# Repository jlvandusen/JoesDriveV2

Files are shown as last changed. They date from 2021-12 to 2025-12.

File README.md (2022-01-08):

# JoesDriveV2
* Shared Code Base for Joe's Drive V2 using AdaFruit Feather CPUs and SND Boards
* This will support a complete PCB delivered solution to simplify and provide cost savings for future development.
* utilizes ESP32 and Feather based CPUs
* Simplified but adaptable Dome Controls
* Land, Sea and Air control schemas supporting Wifi, BT and more...
* This will contain all the code for my Joe's drive V2 setup.

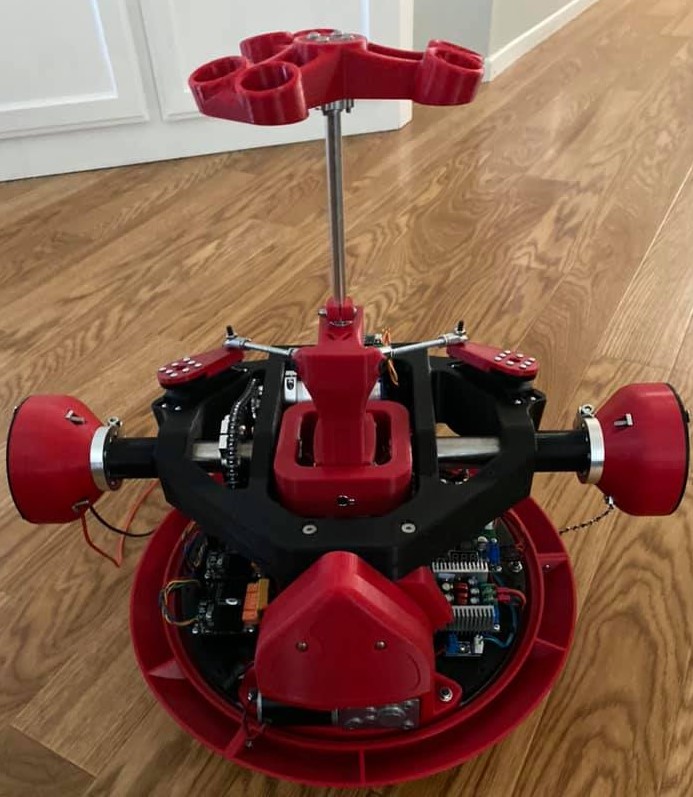
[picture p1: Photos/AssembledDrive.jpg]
JoesDrivev2


## Hardware setup
This drive is everything including the kitchen sink, remote starter, easy to configure ESP32 to Move or Xbox controllers (no other hardware needed), Single PCB board with all needed connections

### ESP32 Huzzah
The ESP32 Huzzah Feather is the main brains of the drive, and it is responsible for handling the remote functions and reading the IMU sub-board from the serial terminals.

### 32u4 Proto M0
Currently utilizes a second Feather 32u4 M0 for offloading remaining serial ports for Dome specific controls over serial.

### trinket Pro Mini - IMU reader
IMU locks are the thing of the past

### ESP32 Huzzah Dome Controller
Utilizes easy to configure ESPNOW technologies to communicate between body and dome - no more wifi or pairing garbage.

## New Features
The following are the new features that I have added into my drive to make it more usable.
Feature | Description
------- | -----------
All-In_One PCB | The Main board has buck converters built right in with all necessary connections over PIN and JST XH.  48V in and supports 5v, 6v and 9v outputs.
i2c Sound Control | Utilizes standard (non pin triggered) i2c sound controls allowing for full flexibility and adaptable sound choices based on button combination and actions.
CHain Drive! | The main drive is handled by chain drive to solve slipping seen in previous versions as well as to provide a more stable drive experience.
S2S Gearing | Utilizes gear for stable side to side controls (similar to Bruton's design)
ENC Dome Control | Utilizes ENC built in motor controls for exact directional control of dome rotation.
v2 Flywheel | Very low profile (higher than the battery compartment - thus allowing for out of ball testing and weight disbursement.
DFRobot 0601 | Using the DFRobot Motor Driver 0601 H Bridge Motor driver
Mp3 Qwiic/i2c trigger | Code that drives the custom Mp3 trigger for full sound controls via multi combinations

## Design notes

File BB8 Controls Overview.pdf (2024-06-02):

## BB8 SHADOW Movement controls

Your first controller when paired and turned on, will become your drive controller
The second controller when paired and turned on will become your dome controller
Key movement controls explained
You will hold the 2 nav controllers in your left and right hands, for the convenience of this instructional, we will represent your left hand as the dome controls and your right hand as the drive controls.
Movement does not occur until the Drive Safety feature has been enabled. This is done by pressing the PS button the drive controller. It’s a toggle, so pressing will enable or disable the drive systems for safety reasons.

## Drive Controller commands

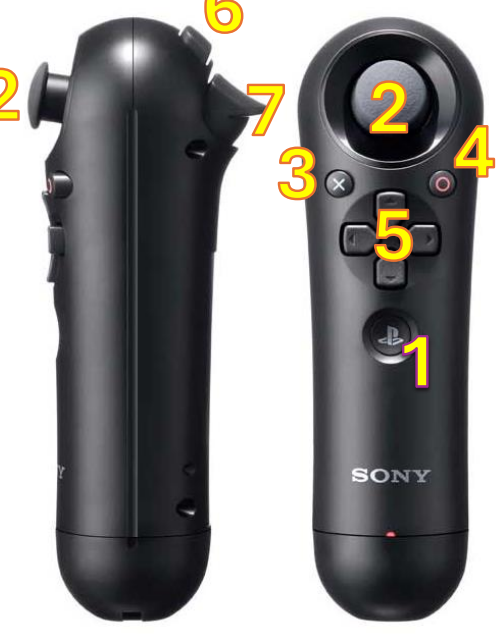
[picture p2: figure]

1. PS = Drive Enable/Disable safety
2. Forward/Backward = Forward or backward drive movement, Left/Right = Side to Side left or right for steering Pressing in the joystick will reverse the drive direction. By default its forward, if pressed will reverse all controls.
3. X =
4. O =
5. Digital pad up, down, left and right will play sounds, NOTE: the pad up will be random sounds.
6. L1 = Modifier (enabling Dome Spin movements)
7. L2 =

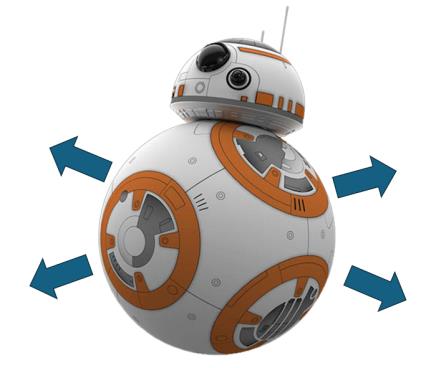
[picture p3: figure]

## Dome Controller commands

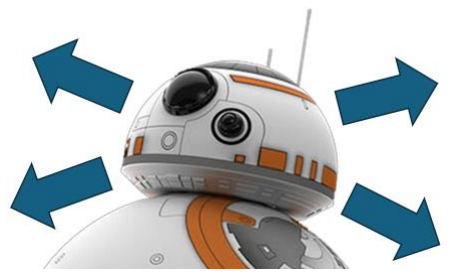
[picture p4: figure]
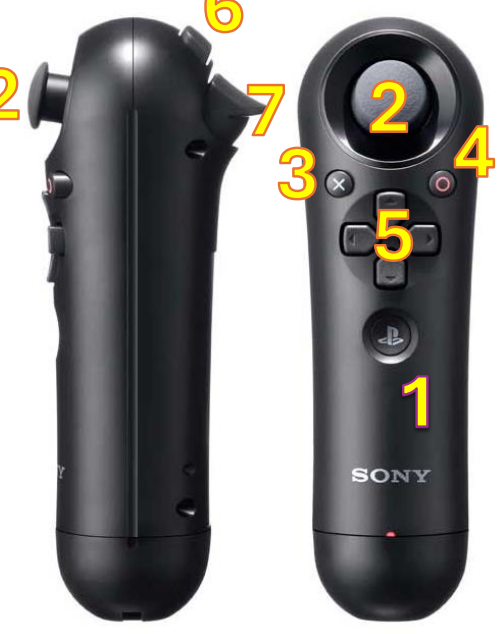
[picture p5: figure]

1. PS = Drive Enable/Disable safety
2. Forward/Backward = Forward or backward dome movement, Left/Right = left and right dome movement. Pressing in the joystick will enable dome servo mode and the navigation now on the drive controller will be forced to turning only left or right 40 degrees from center.
3. X =
4. O =
5. Digital pad up, down, left and right will play sounds, NOTE: the pad up will be random sounds.
6. L1 = Modifier (enabling Gyro movements using the drive controller left or right)
7. L2 =

### Saving offsets

When pressing digital pad (5) up on both controllers, will enable save of all current placements (potentiometer and IMU offsets).

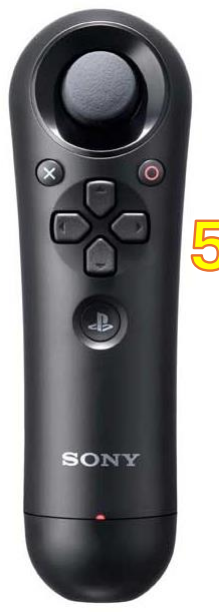
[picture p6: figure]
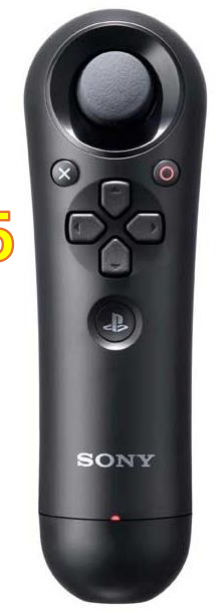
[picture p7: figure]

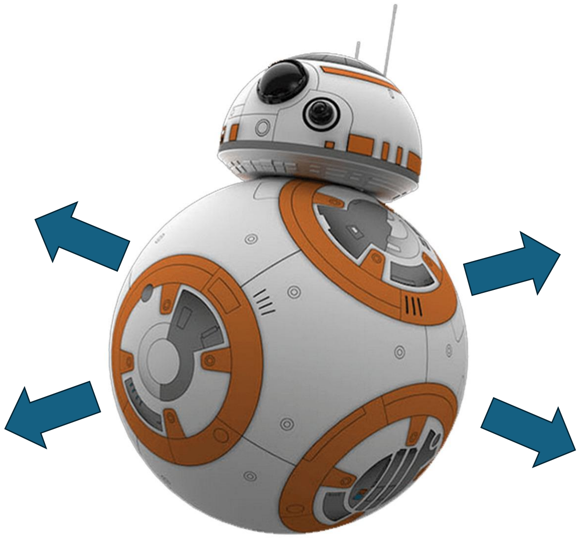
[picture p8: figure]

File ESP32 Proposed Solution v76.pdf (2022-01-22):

# Joe’s Drive v2

# The Solution consists of 3 PCB boards

1. Main Board – this regulates power from a single 48v - 12v battery to 5v, 6v or 9v outputs, it has all the necessary connectors to quickly wire to DFRobot H Bridge motor controllers and all required sensors. It utilizes 2 CPUs which segregate duties between dome or main body related motors and sensors
(Feather 32u4 Proto M0 or 32u4 Basic Proto | Feather 32u4 RF Series AND Feather ESP32 HUZZAH Series processors).

NOTE: There are 6 options given depending upon secondary 32u4 and which MP3 trigger you wish to use

2. IMU/MPU Board – this connects via Serial and consists of dedicated CPU (trinket m0) as well as MPU6050 series that regulates Pitch, Tilt and yaw movement on the system.
3. Dome board – this communicates via ESP32NOW to the Main Board and controls LEDs in the dome only. Future adaption of motion sensor and distance sensors.

# Version 7.1/7.5/7.6

# OPTION 1: 32u4 PROTO M0 and i2C MP3 Trigger

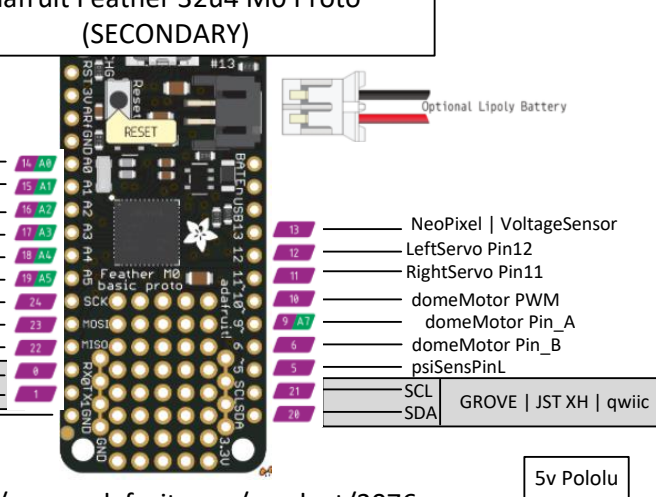
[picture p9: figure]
NeoPixel | VoltageSensor; domeMotor Pin_B; domeMotor Pin_A; psiSensPinL; LeftServo Pin12 RightServo Pin11 domeMotor PWM; SCL; SDA; GROVE | JST XH | qwiic; 5v Pololu; (SECONDARY)
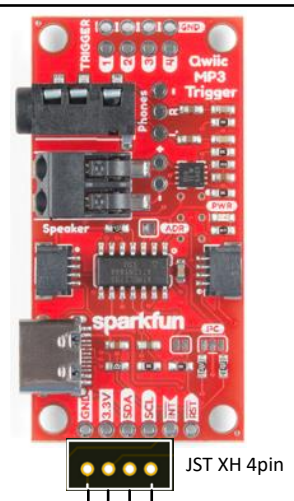
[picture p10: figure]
JST XH 4pin
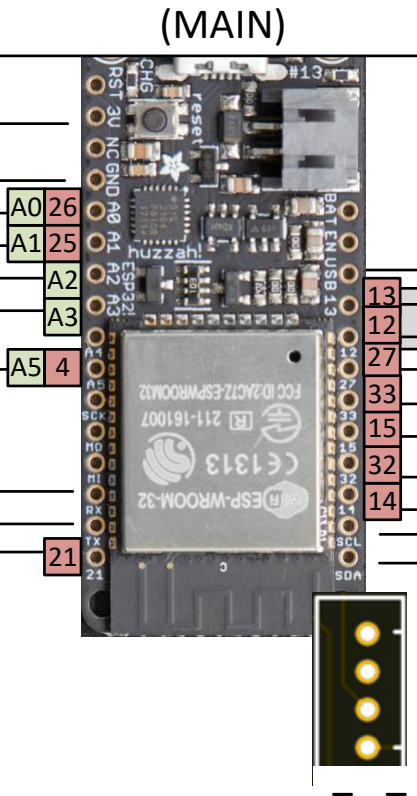
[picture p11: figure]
(MAIN)

S2SPOT

drivepin1

S2SPin1

drivepin2

S2SPin2

Trinket
(Serial1)

To 32u4
(Serial2)

MotorEncPinA
MotorEncPinB

VCCSensor

HallMonitor

To ESP32
(Serial1)

ESP32
(Serial1)

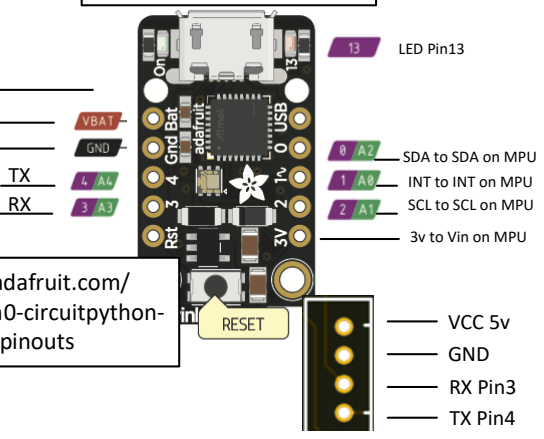
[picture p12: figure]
SCL to SCL on MPU; SDA to SDA on MPU; INT to INT on MPU; 3v to Vin on MPU; TX Pin4; RX Pin3; GND; VCC 5v; LED Pin13

TX

## MPU6050

## Adafruit Trinket M0

5V

GND

SCL

SDA

5v

https://learn.adafruit.com/mpu6050-6-dof-accelerometer-and-gyro/pinouts

https://learn.adafruit.com/adafruit-trinket-m0-circuitpython-arduino/pinouts

GND

INT

i2C

12/24/48v In
5v Out

GND Out
GND In

Bat on 32u4,
Trinket and
ESP32
And Outputs

S2S_PWM

Drive_PWM

GND

+ 3.3v

+5v Input

## https://www.adafruit.com/product/3076

lLogicPIN

battPin (26)
psiPIN (25)

(Serial1)

sLogicPIN

GND

## Adafruit ESP32 HUZZAH32 Feather (DOME)

FlyMotor PWM
FlyMotor Pin_A
FlyMotor Pin_B
SCL
SDA
GND

GND 3.3V SDA SCL
To Feather 32u4

Sparkfun QWIIC MP3 TRIGGER

VCC 5v

GND

TX Pin17 ESP32

RX Pin16 ESP32

## To Trinket (MPU)

## To ESP32 (MAIN)

12/24/48v In
9v/6v Out

GND Out
GND In

To Left/Right
Servo and
Output

6v/9v Pololu

## Adafruit ESP32 HUZZAH32 Feather

## Adafruit Feather 32u4 M0 Proto

# OPTION 2: 32u4 Basic Proto and i2C MP3 Trigger

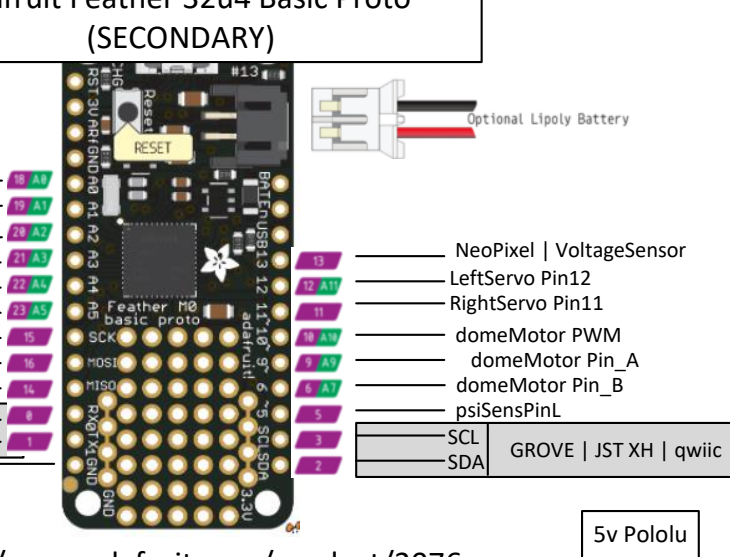
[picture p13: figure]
NeoPixel | VoltageSensor; domeMotor Pin_B; domeMotor Pin_A; psiSensPinL; LeftServo Pin12 RightServo Pin11 domeMotor PWM; SCL; SDA; GROVE | JST XH | qwiic; 5v Pololu; (SECONDARY)

S2SPOT

drivepin1

S2SPin1

drivepin2

S2SPin2

Trinket
(Serial1)

To 32u4
(Serial2)

MotorEncPinA
MotorEncPinB

VCCSensor

HallMonitor

To ESP32
(Serial1)

ESP32
(Serial1)

TX

## MPU6050

## Adafruit Trinket M0

5V

GND

SCL

SDA

5v

https://learn.adafruit.com/mpu6050-6-dof-accelerometer-and-gyro/pinouts

https://learn.adafruit.com/adafruit-trinket-m0-circuitpython-arduino/pinouts

GND

INT

i2C

12/24/48v In
5v Out

GND Out
GND In

Bat on 32u4,
Trinket and
ESP32
And Outputs

S2S_PWM

Drive_PWM

GND

+ 3.3v

+5v Input

## https://www.adafruit.com/product/3076

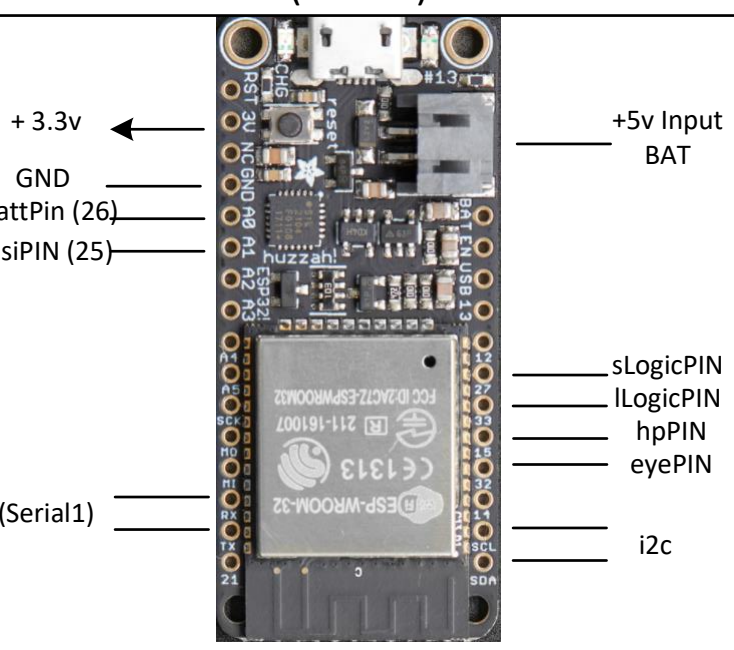
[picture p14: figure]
+5v Input; BAT; hpPIN eyePIN

lLogicPIN

battPin (26)
psiPIN (25)

(Serial1)

sLogicPIN

GND

## Adafruit ESP32 HUZZAH32 Feather (DOME)

FlyMotor PWM
FlyMotor Pin_A
FlyMotor Pin_B
SCL
SDA
GND

GND 3.3V SDA SCL
To Feather 32u4

Sparkfun QWIIC MP3 TRIGGER

VCC 5v

GND

TX Pin17 ESP32

RX Pin16 ESP32

## To Trinket (MPU)

## To ESP32 (MAIN)

12/24/48v In
9v/6v Out

GND Out
GND In

To Left/Right
Servo and
Output

6v/9v Pololu

## Adafruit ESP32 HUZZAH32 Feather

## Adafruit Feather 32u4 Basic Proto

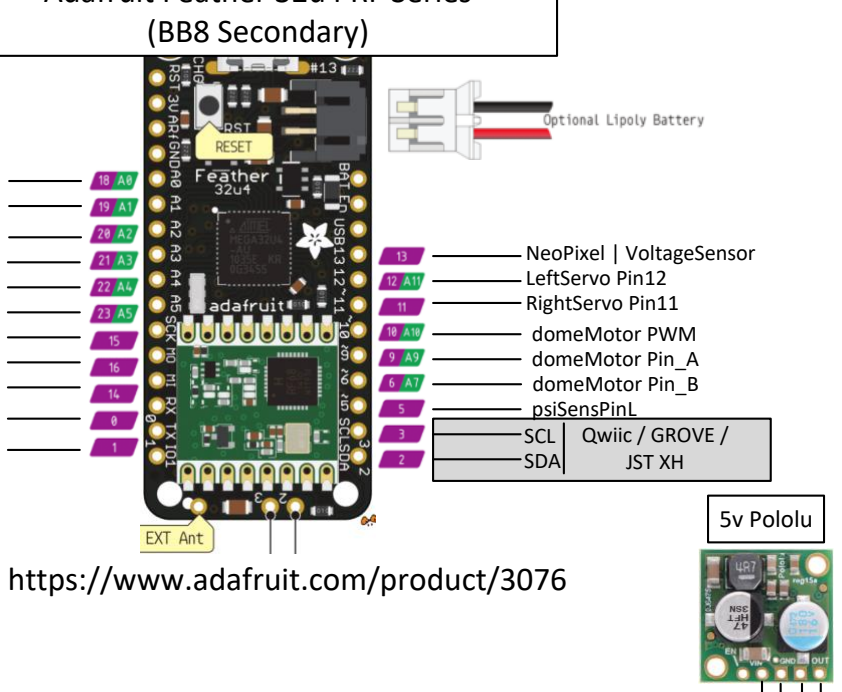
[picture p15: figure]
NeoPixel | VoltageSensor; domeMotor Pin_B; domeMotor Pin_A; psiSensPinL; LeftServo Pin12 RightServo Pin11 domeMotor PWM; https://www.adafruit.com/product/3076; SCL SDA; Qwiic / GROVE / JST XH; 5v Pololu; (BB8 Secondary)

MotorEncPinA
MotorEncPinB
HallMonitor

ESP32
(Serial1)

# OPTION 3: 32u4 RF and i2C MP3 Trigger

S2SPOT

drivepin1

S2SPin1

drivepin2

S2SPin2

Trinket
(Serial1)

To 32u4
(Serial2)

ESP32
(Serial1)

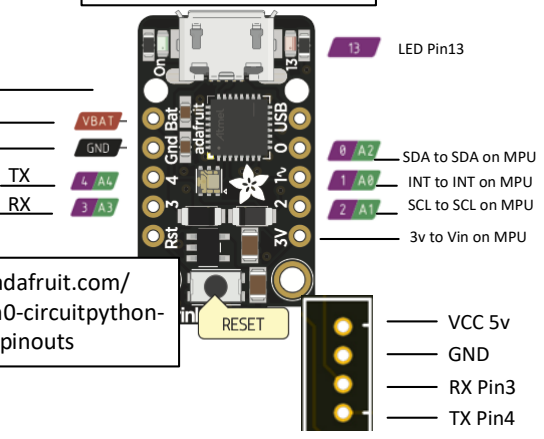
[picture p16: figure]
SCL to SCL on MPU; SDA to SDA on MPU; INT to INT on MPU; 3v to Vin on MPU; TX Pin4; RX Pin3; GND; VCC 5v; LED Pin13

TX

## MPU6050

## Adafruit Trinket M0

5V

GND

SCL

SDA

5v

https://learn.adafruit.com/mpu6050-6-dof-accelerometer-and-gyro/pinouts

https://learn.adafruit.com/adafruit-trinket-m0-circuitpython-arduino/pinouts

GND

INT

i2C

12/24/48v In
5v Out

GND Out
GND In

Bat on 32u4,
Trinket and
ESP32
And Outputs

S2S_PWM

Drive_PWM

GND

+ 3.3v

+5v Input

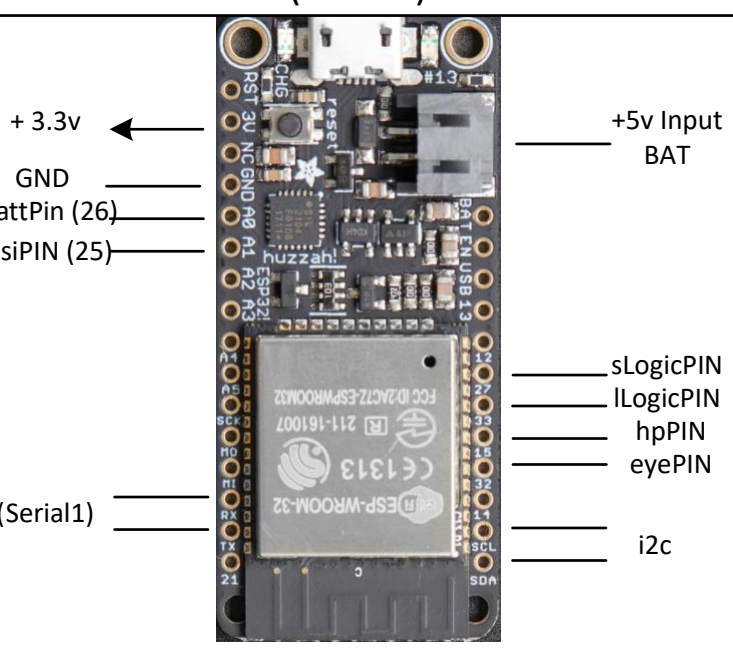
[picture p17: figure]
+5v Input; BAT; hpPIN eyePIN

lLogicPIN

battPin (26)
psiPIN (25)

(Serial1)

sLogicPIN

GND

## Adafruit ESP32 HUZZAH32 Feather (DOME)

FlyMotor PWM
FlyMotor Pin_A
FlyMotor Pin_B
SCL
SDA
GND 3.3V SDA SCL
To Feather 32u4

Sparkfun QWIIC MP3 TRIGGER

VCC 5v

GND

TX Pin17 ESP32

RX Pin16 ESP32

## To Trinket (MPU)

## To ESP32 (MAIN)

12/24/48v In
9v/6v Out

GND Out
GND In

To Left/Right
Servo and
Output

6v/9v Pololu

## Adafruit ESP32 HUZZAH32 Feather Adafruit Feather 32u4 RF Series

# OPTION 4: 32u4 PROTO M0 and ADAFRUIT MUSIC MAKER FEATHERWING

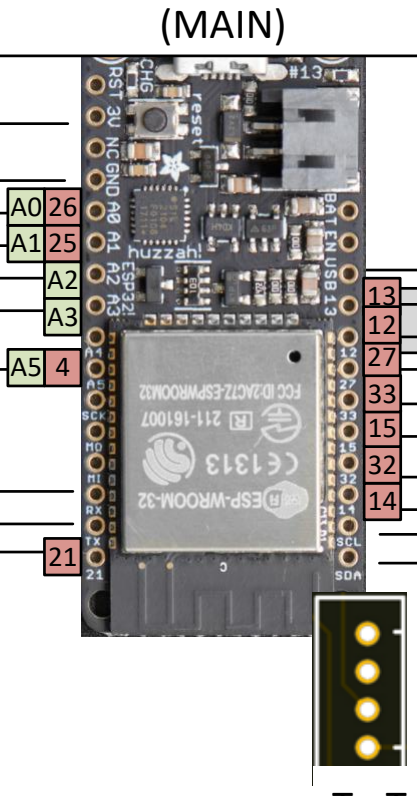
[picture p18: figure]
(MAIN)

S2SPOT

drivepin1

S2SPin1

drivepin2

S2SPin2

Trinket
(Serial1)

To 32u4
(Serial2)

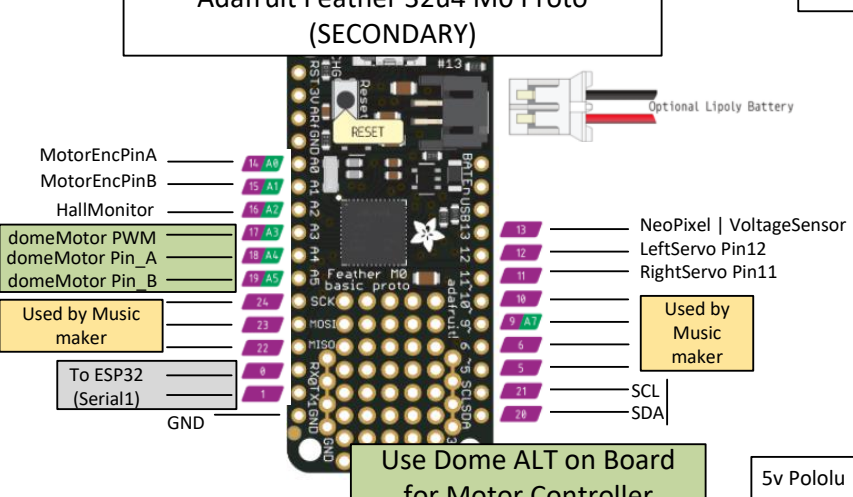
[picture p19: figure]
NeoPixel | VoltageSensor; domeMotor Pin_A; LeftServo Pin12; RightServo Pin11; To ESP32 (Serial1); SCL SDA; GND; 5v Pololu; (SECONDARY); domeMotor PWM; Use Dome ALT on Board; Used by Music maker

MotorEncPinA
MotorEncPinB

domeMotor Pin_B

HallMonitor

ESP32
(Serial1)

TX

## MPU6050

## Adafruit Trinket M0

5V

GND

SCL

SDA

5v

https://learn.adafruit.com/mpu6050-6-dof-accelerometer-and-gyro/pinouts

https://learn.adafruit.com/adafruit-trinket-m0-circuitpython-arduino/pinouts

GND

INT

i2C

12/24/48v In
5v Out

GND Out
GND In

Bat on 32u4,
Trinket and
ESP32
And Outputs

S2S_PWM

Drive_PWM

GND

+ 3.3v

+5v Input

lLogicPIN

battPin (26)
psiPIN (25)

(Serial1)

sLogicPIN

GND

## Adafruit ESP32 HUZZAH32 Feather (DOME)

FlyMotor PWM
FlyMotor Pin_A
FlyMotor Pin_B
SCL
SDA

ADAFRUIT VS105 Feather

VCC 5v

GND

TX Pin17 ESP32

RX Pin16 ESP32

## To Trinket (MPU)

## To ESP32 (MAIN)

12/24/48v In
9v/6v Out

GND Out
GND In

To Left/Right
Servo and
Output

6v/9v Pololu

## Adafruit ESP32 HUZZAH32 Feather

## Adafruit Feather 32u4 M0 Proto

## for Motor Controller

X
X
X

X
X
X
X

# OPTION 5: 32u4 Basic Proto and ADAFRUIT MUSIC MAKER FEATHERWING

S2SPOT

drivepin1

S2SPin1

drivepin2

S2SPin2

Trinket
(Serial1)

To 32u4
(Serial2)

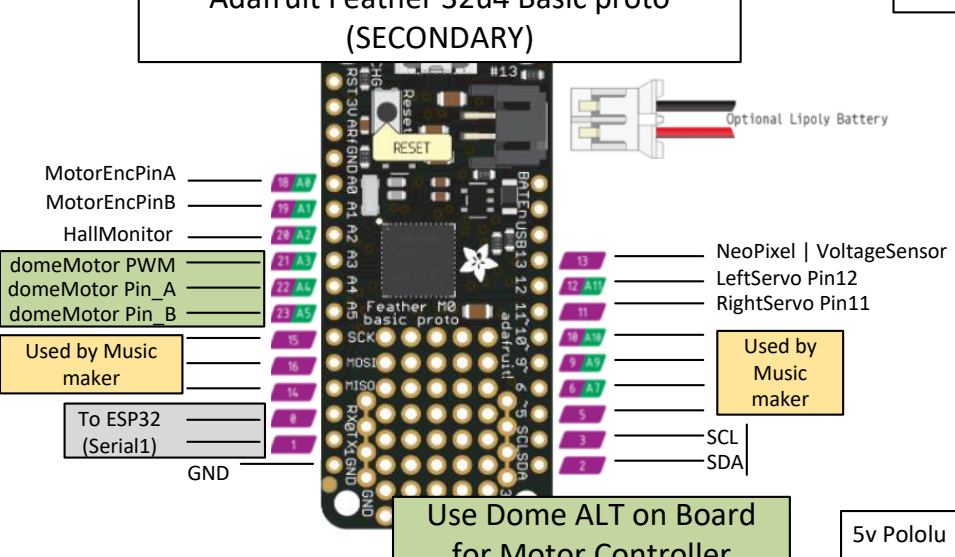
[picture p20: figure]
NeoPixel | VoltageSensor; domeMotor Pin_A; LeftServo Pin12; RightServo Pin11; To ESP32 (Serial1); SCL SDA; GND; 5v Pololu; (SECONDARY); domeMotor PWM; Use Dome ALT on Board; Used by Music maker

MotorEncPinA
MotorEncPinB

domeMotor Pin_B

HallMonitor

ESP32
(Serial1)

TX

## MPU6050

## Adafruit Trinket M0

5V

GND

SCL

SDA

5v

https://learn.adafruit.com/mpu6050-6-dof-accelerometer-and-gyro/pinouts

https://learn.adafruit.com/adafruit-trinket-m0-circuitpython-arduino/pinouts

GND

INT

i2C

12/24/48v In
5v Out

GND Out
GND In

Bat on 32u4,
Trinket and
ESP32
And Outputs

S2S_PWM

Drive_PWM

GND

+ 3.3v

+5v Input

lLogicPIN

battPin (26)
psiPIN (25)

(Serial1)

sLogicPIN

GND

## Adafruit ESP32 HUZZAH32 Feather (DOME)

FlyMotor PWM
FlyMotor Pin_A
FlyMotor Pin_B
SCL
SDA

ADAFRUIT VS105 Feather

VCC 5v

GND

TX Pin17 ESP32

RX Pin16 ESP32

## To Trinket (MPU)

## To ESP32 (MAIN)

12/24/48v In
9v/6v Out

GND Out
GND In

To Left/Right
Servo and
Output

6v/9v Pololu

## Adafruit ESP32 HUZZAH32 Feather

## Adafruit Feather 32u4 Basic proto

## for Motor Controller

X
X
X

X
X
X
X

# OPTION 6: 32u4 Basic Proto and i2C MP3 Trigger from Zio

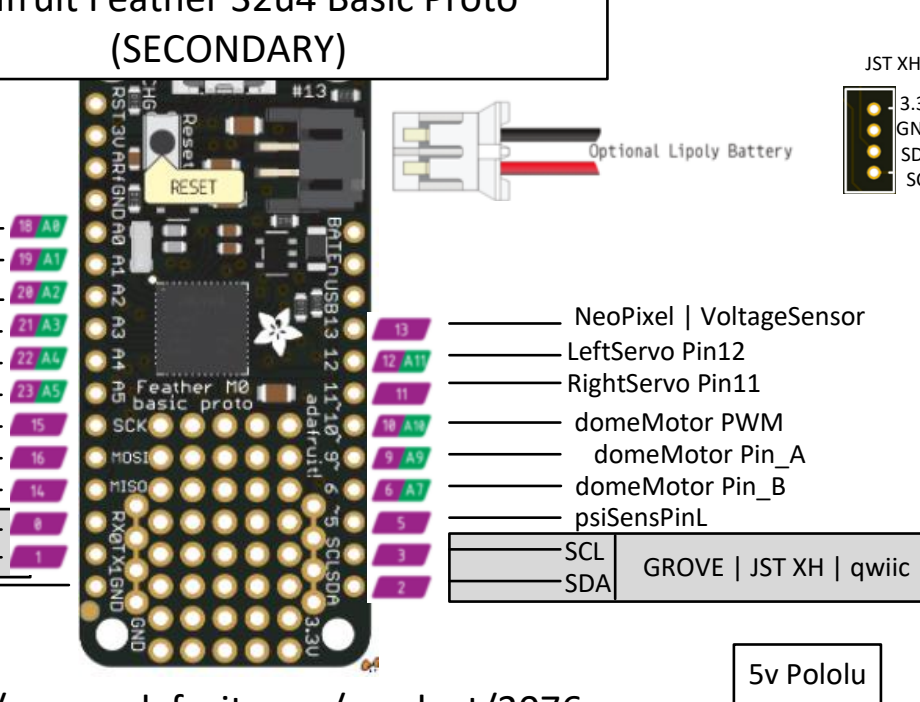
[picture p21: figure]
NeoPixel | VoltageSensor; domeMotor Pin_B; domeMotor Pin_A; psiSensPinL; LeftServo Pin12 RightServo Pin11 domeMotor PWM; SCL; SDA; GROVE | JST XH | qwiic; 5v Pololu; (SECONDARY)

S2SPOT

drivepin1

S2SPin1

drivepin2

S2SPin2

Trinket
(Serial1)

To 32u4
(Serial2)

MotorEncPinA
MotorEncPinB

VCCSensor

HallMonitor

To ESP32
(Serial1)

ESP32
(Serial1)

TX

## MPU6050

## Adafruit Trinket M0

5V

GND

SCL

SDA

5v

https://learn.adafruit.com/mpu6050-6-dof-accelerometer-and-gyro/pinouts

https://learn.adafruit.com/adafruit-trinket-m0-circuitpython-arduino/pinouts

GND

INT

i2C

12/24/48v In
5v Out

GND Out
GND In

Bat on 32u4,
Trinket and
ESP32
And Outputs

S2S_PWM

Drive_PWM

GND

+ 3.3v

+5v Input

## https://www.adafruit.com/product/3076

lLogicPIN

battPin (26)
psiPIN (25)

(Serial1)

sLogicPIN

GND

## Adafruit ESP32 HUZZAH32 Feather (DOME)

FlyMotor PWM
FlyMotor Pin_A
FlyMotor Pin_B
SCL
SDA
GND

3.3v
GND
SDA
SCL

JST XH 4pin

To Feather 32u4

Zio QWIIC MP3 TRIGGER

VCC 5v

GND

TX Pin17 ESP32

RX Pin16 ESP32

## To Trinket (MPU)

## To ESP32 (MAIN)

12/24/48v In
9v/6v Out

GND Out
GND In

To Left/Right
Servo and
Output

6v/9v Pololu

## Adafruit ESP32 HUZZAH32 Feather

## Adafruit Feather 32u4 Basic Proto

Qwiic to
GROVE
Connector

## MOTOR DRIVER 1

## MOTOR DRIVER 2

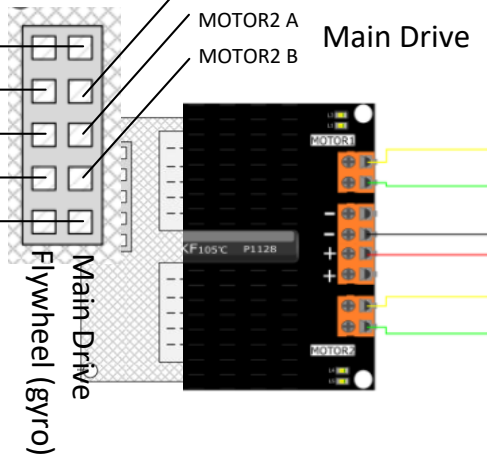
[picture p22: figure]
MOTOR2 A; MOTOR2 B; Main Drive; Flywheel (gyro)

VCC 3.3v

GND

VCC 3.3v

GND

## S2S Motor

## Flywheel (gyro)

## Main Drive

## VCC 12/24v

## VCC 12/24v

MOTOR1 A

MOTOR1 B

## Flywheel (gyro)

MOTOR1 A

MOTOR1 B

## Head Spin

MOTOR1 PWM

MOTOR2 PWM

MOTOR1 PWM

MOTOR2 PWM

#define S2S_pwm 33 // SCL 22 and SDA 23 #define S2S_pin_1 26 //A0

#define S2S_pin_2 25 //A1

#define Drive_pwm 21 // SCL 22 and SDA 23 #define Drive_pin_1 4

#define Drive_pin_2 27

#define domeMotor_pwm 21

#define domeMotor_pin_A 22 #define domeMotor_pin_B 23

ALT w/ MUSIC MAKER FEATHERWING #define domeMotor_pwm A3
#define domeMotor_pin_A A4 #define domeMotor_pin_B A5

#define flyWheelMotor_pwm 15 #define flyWheelMotor_pin_A 32 #define flyWheelMotor_pin_B 14

32u4

## ESP32

## ESP32

## ESP32

## DOME Motor

## To Trinket (MPU)

GND TX
Pin17
ESP32

RX
Pin16
ESP32

VCC 24v to Buck Convertors

GND

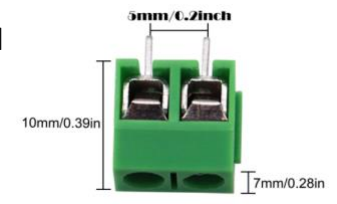
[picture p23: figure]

## Screw Terminal INPUT

## S2S Motor

PinA0
ESP32

PinA1
ESP32

## Drive Motor

Pin4
ESP32

Pin21
ESP32

## S2S POT

VCC
3.3v

PinA2
ESP32

## NEOPIX

VCC
5v Buck

Pin27
ESP32 GND

VCC 5v from Buck Convertors

GND

## Screw Terminal 5v Output

VCC 6v from Buck Convertors

GND

## Screw Terminal 6v Output

## To DomeSpin

VCC
5v GND
Pin3
32u4

Pin2
32u4

## Future

Pin5
32u4

Pin21
32u4

Pin22
ESP32
SCL

Pin23
ESP32
SDA

## Gyro / Fly

Pin9
32u4

Pin6
32u4

## Dome Motor

Pin10
32u4

Pin13
32u4

## Right Servo

Pin 11
32u4 | VCC
| 9v
| From
| Buck

GND

## Left Servo

Pin 12
32u4 | VCC
| 9v
| From
| Buck

GND

## PSI Sensor

Pin20
32u4

Pin18
32u4

## Hall Sensor

Pin 19
32u4

GND

VCC
3.3v

GND

## VCC Sensor

Pin22
32u4 GND

https://www.amazon.com/
s?k=2+Pin+%26+3+Pin+5mm%2F0. 2inch+Pitch+PCB+Mount&i=industr ial&ref=nb_sb_noss

## JST-XH 2.54mm

## i2c ESP32

GND
ESP32
GND
Motor Driver 1 | Motor Driver 2

VCC
32U4
3.3V

GND
GND

Pin21
32u4

Pin22
32u4

Pin23
32u4

Pin15
ESP32

VCC
Esp32
3.3V

Pin32
ESP32

Pin14
ESP32

VCC
5v

## Drive

## GYRO

S2S

## Dome 1

1

VCC 9v from Buck Convertors

GND

## Screw Terminal 9v Output

RX TX

## Serial Debug

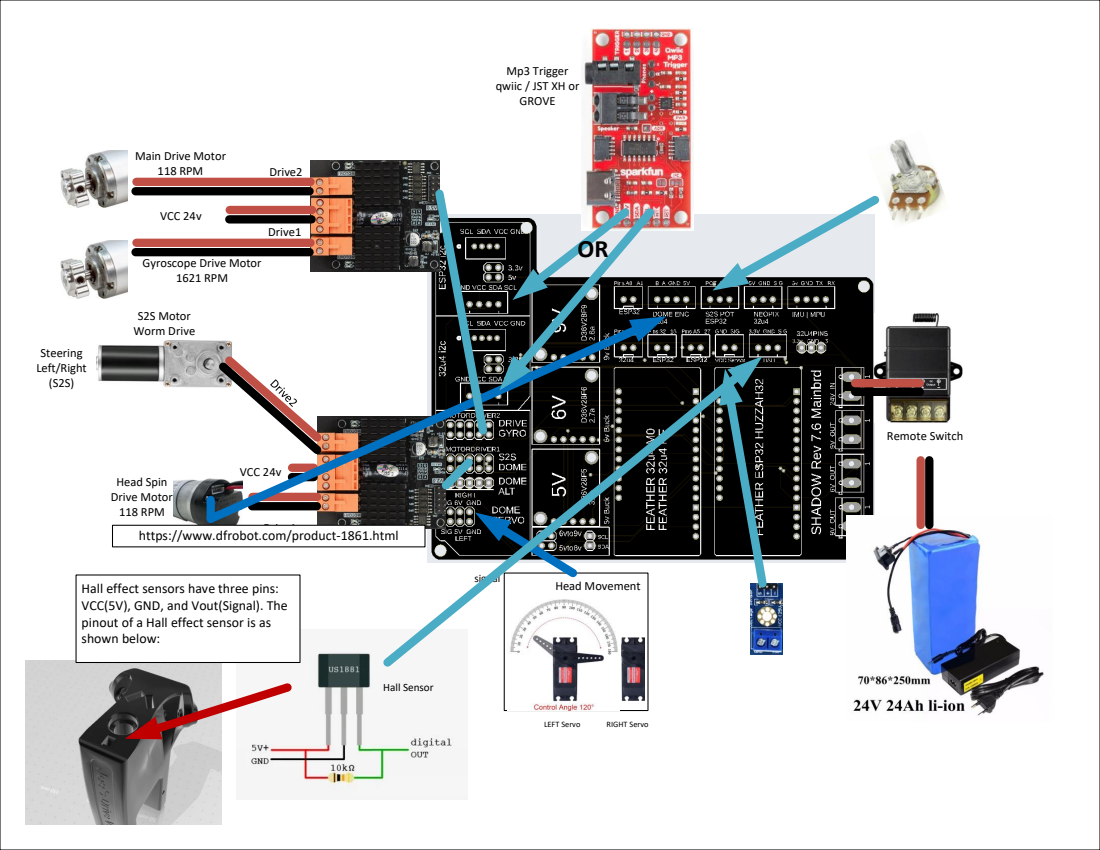
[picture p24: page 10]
Head Movement; Remote Switch; LEFT Servo; RIGHT Servo; S2S Motor Worm Drive; Drive1; Drive2; Steering Left/Right (S2S); signal; VCC 24v; Hall Sensor

Mp3 Trigger
qwiic / JST XH or
GROVE

Main Drive Motor
118 RPM

Gyroscope Drive Motor
1621 RPM

Head Spin
Drive Motor
https://www.dfrobot.com/product-1861.html

Hall effect sensors have three pins:
VCC(5V), GND, and Vout(Signal). The
pinout of a Hall effect sensor is as
shown below:

# MAIN BOARD 7.1/7.5

## StepDowns

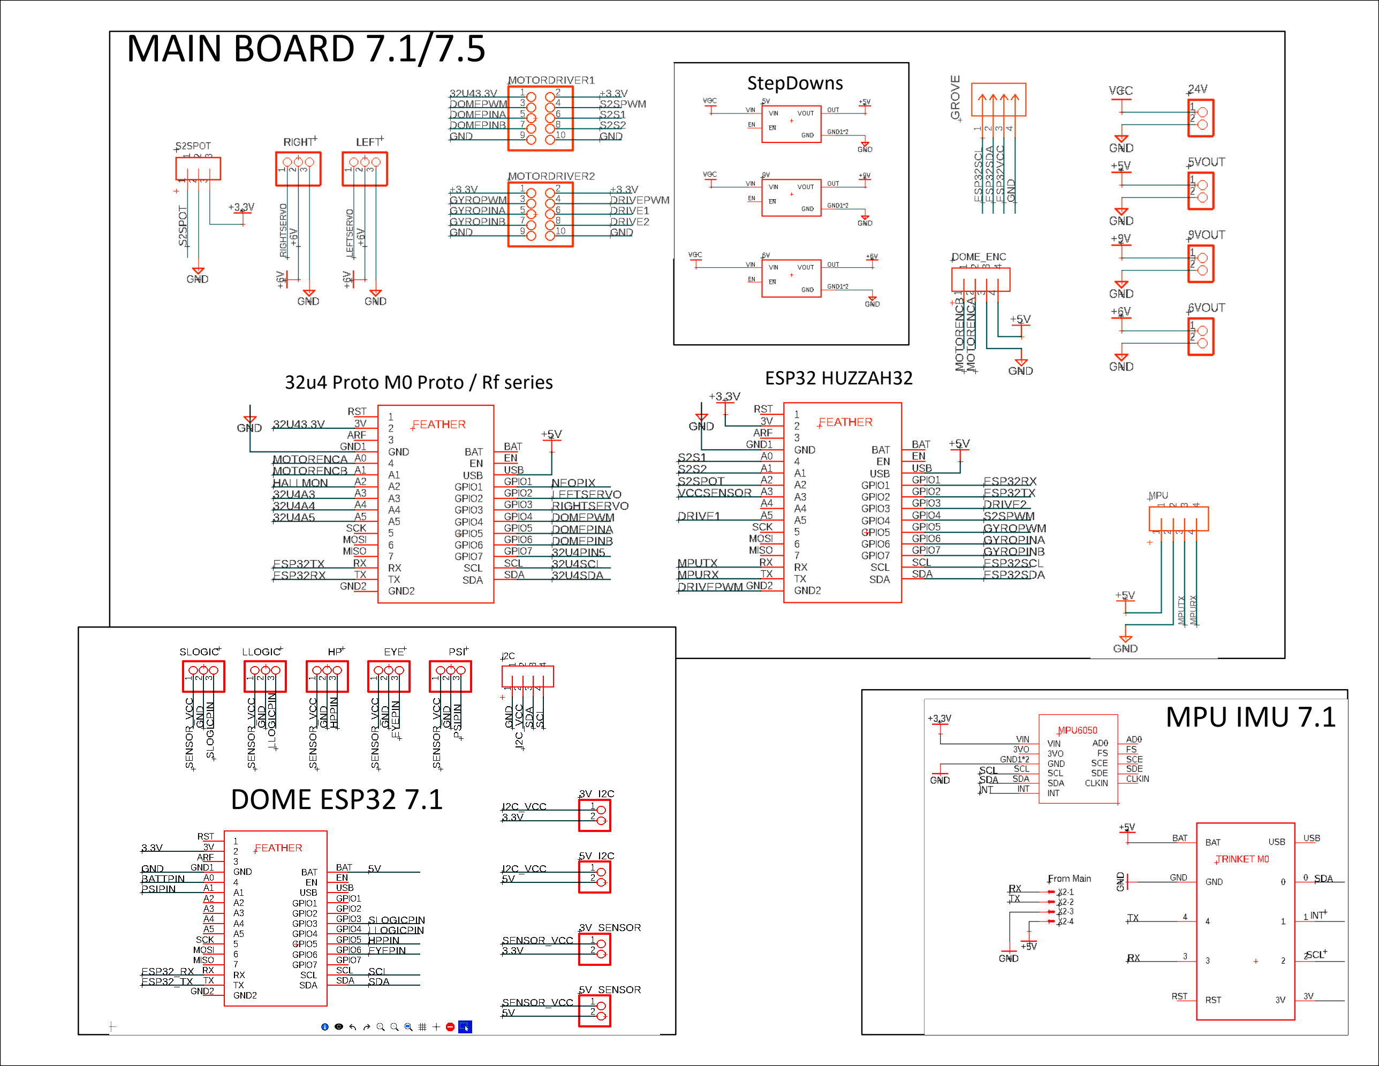
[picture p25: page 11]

# MPU IMU 7.1

# DOME ESP32 7.1

32u4 Proto M0 Proto / Rf series | ESP32 HUZZAH32

+5v Input; BAT; hpPIN eyePIN

lLogicPIN

battPin (26)
psiPIN (25)

eyeLED Single

(Serial1)

sLogicPIN

GND

## Adafruit ESP32 HUZZAH Feather (BB8 Dome)

HP (hpPIN)
Holo
Single

psiPIN (25)
PSILED
Single

eyePIN

sLogicPIN
sLOGIC
3 lights

lLogic
6 lights

18mm

80mm

Sensor:; MPU6050_A; Type:; Acceleration (m/s2); Driver Ver: 1 Unique ID: 1617 Min Value: -156.91 Max Value: 156.91 Resolution: 0.06 ------------------------------------; MPU6050_G; Gyroscopic (rad/s); Driver Ver: 1 Unique ID: 1618 Min Value: -34.91 Max Value: 34.91 Resolution: 0.00 ------------------------------------

IMU BOARD with TRINKET as CPU

80mm

# IMU BOARD with ProMicro as CPU

i2C via; qwiic

# MAIN BOARD Revision 7.1


# IMU/MPU Board(s)

# Dome Board

# Main Board

## Important Changes:

## - Focused on i2c with grove and jst-xh connectors for the ESP32

# MAIN BOARD Revision 7.5


# IMU/MPU Board(s)

# Dome Board

# Main Board

## Important Changes:

## - Reversed position of the 2 Feathers to allow clearance for the Serial ports - Added ALT position for Dome Motor to allow for

Featherwing (MP3) on secondary feather.

## - Changed the Dome Servos to 2x3 pin header for

easier soldering and space saving.

# MAIN BOARD Revision 7.6


# IMU/MPU Board(s)

# Dome Board

# Main Board

## Important Changes:

## - Added 2nd GROVE for 32u4 supported MP3 - Added 2x2pin headers to ease soldering for: - I2c VCCs - BUCK VCCs

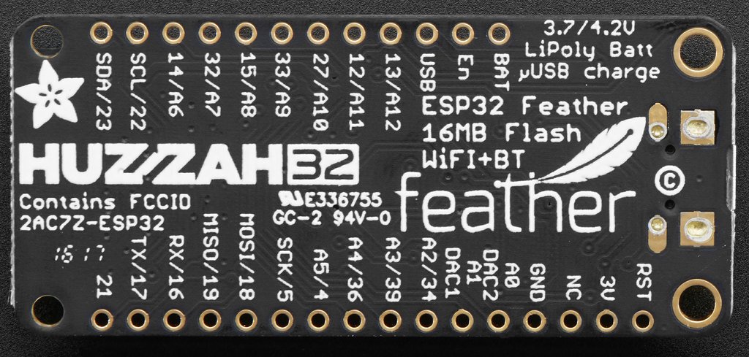
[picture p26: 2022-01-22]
Photos/ESP32HUZZAH_feather_pinoutbot.jpg

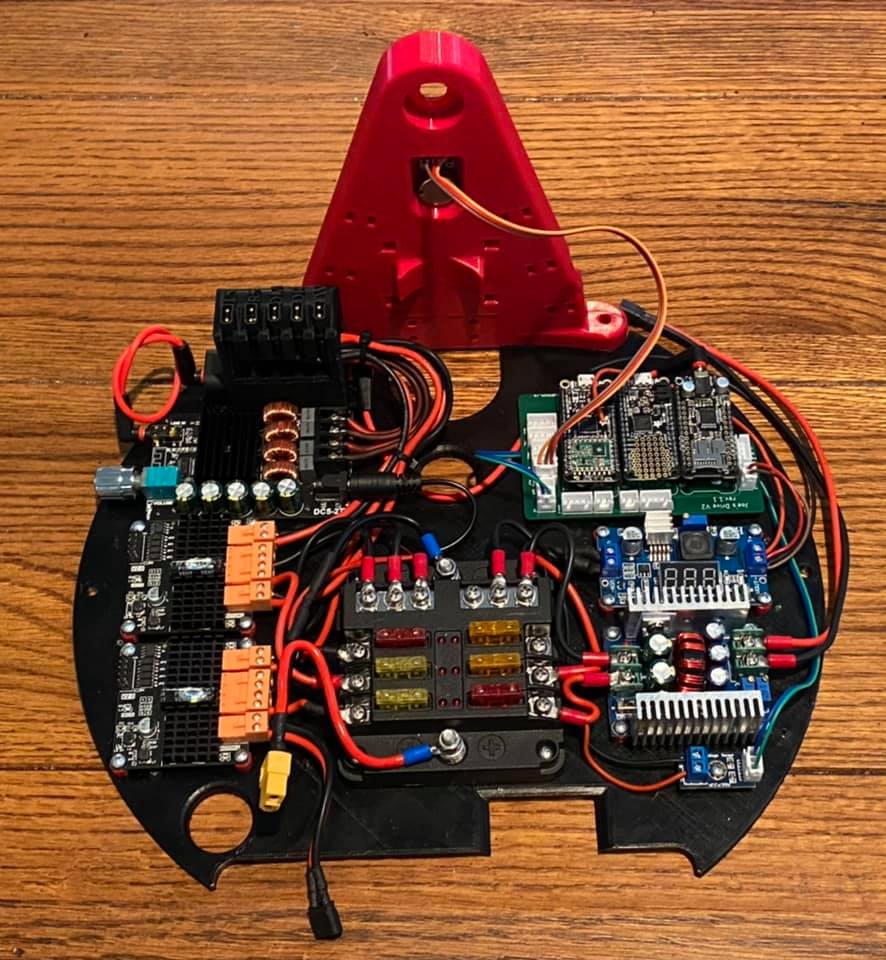
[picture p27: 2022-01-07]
Photos/141859393_2993407897559045_2799193328510504908_n.jpg

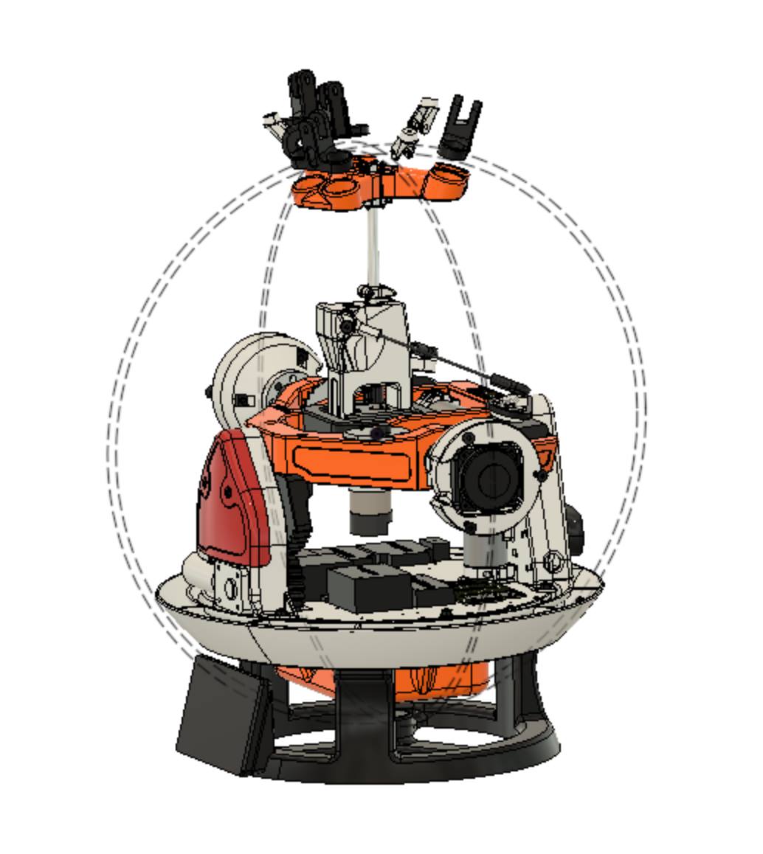
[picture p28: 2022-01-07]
Photos/146278801_4037437846289766_7971786754029637150_n.jpg

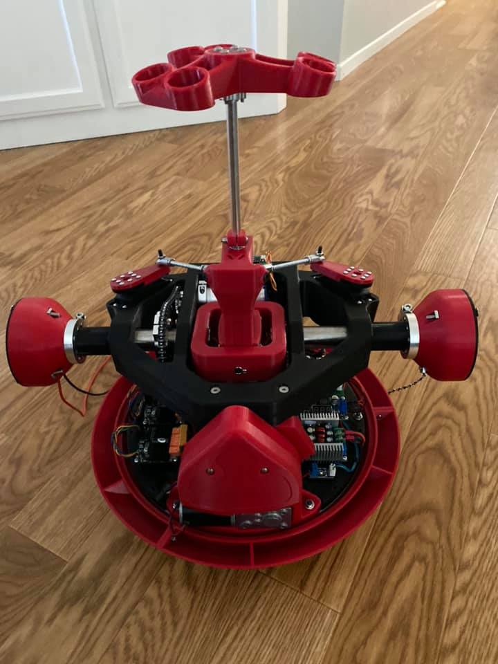
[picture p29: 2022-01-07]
Photos/144482975_2998532313713270_9103672268461786970_n.jpg

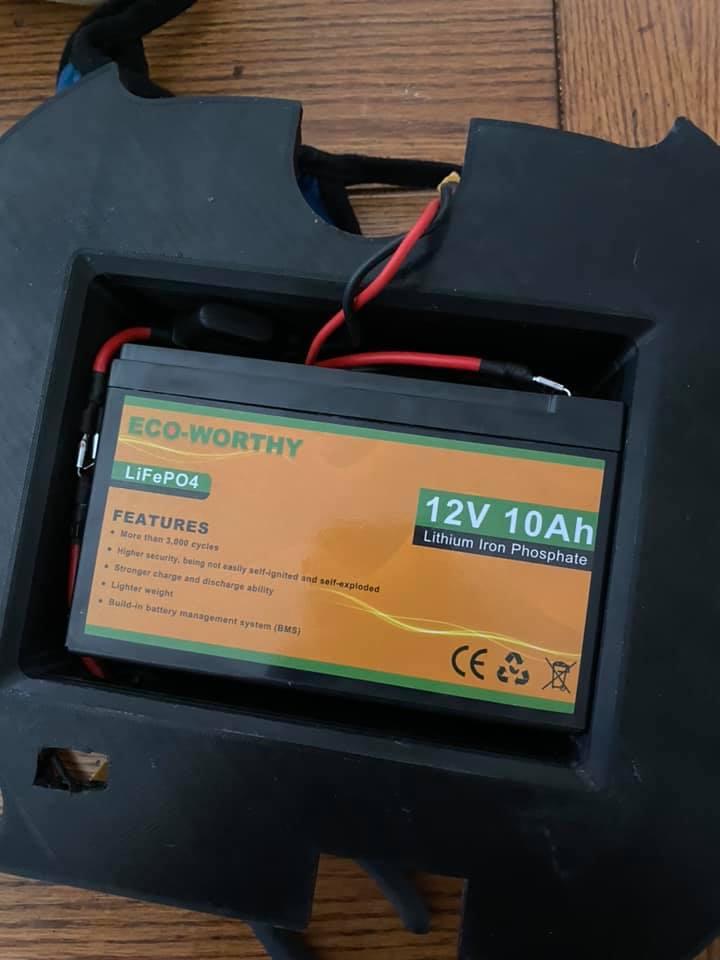
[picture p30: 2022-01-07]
Photos/145721631_2999179536981881_1641464122021647967_n.jpg

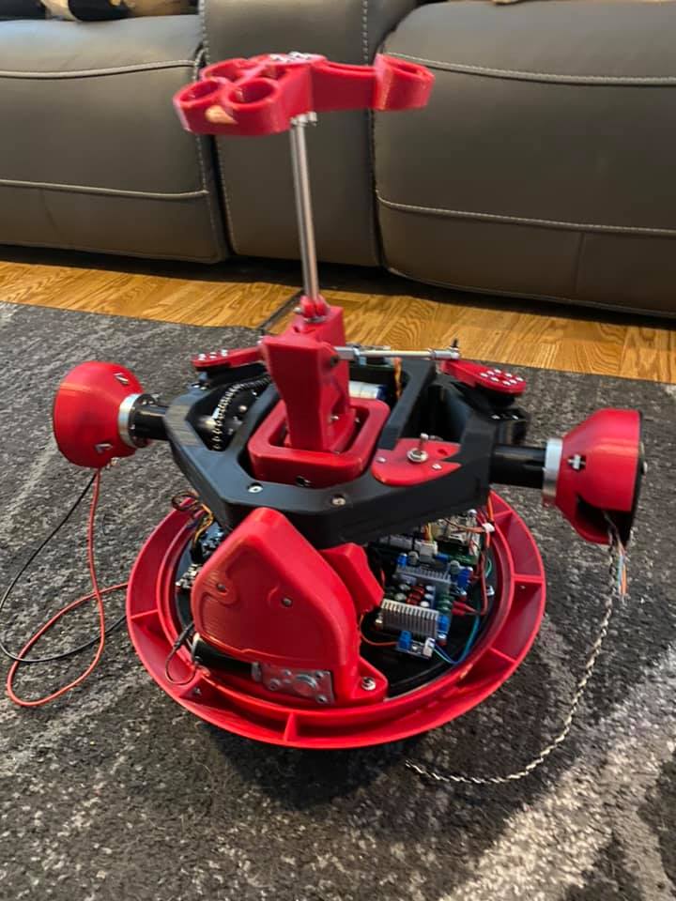
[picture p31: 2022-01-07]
Photos/142579606_2994761294090372_8984235602314645554_n.jpg

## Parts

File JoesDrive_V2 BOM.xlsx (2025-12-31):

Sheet: Sheet 1
BOM
Part | Total needed | Purchase | Cost per | Cost total | URL | Total: |  | $1243.33
ADAFRUIT
Adafruit Feather 32u4 RFM69HCW Packet Radio - 868 or 915 MHz - RadioFruit | 1 | 1 | $24.95 | $24.95 | https://www.adafruit.com/product/5000 |  | https://www.adafruit
Or you can Purchase Adafruit Feather Proto M0 | 1 | 1 | $19.95 | $19.95 | https://www.adafruit.com/product/2771
Hall effect Sensor | 1 | 1 | $2.00 | $2.00 | https://www.adafruit.com (https://www.adafruit.com/product/158) |  | https://www.adafruit
Assembled Adafruit HUZZAH32 – ESP32 Feather Board - with Stacking Headers | 2 | 2 | $21.95 | $43.90 | https://www.adafruit.com (https://www.adafruit.com/product/3619) |  | https://www.adafruit
MPU | 1 | 1 | $6.95 | $6.95 | https://www.adafruit.com (https://www.adafruit.com/product/3886) |  | https://www.adafruit
Trinket m0 | 1 | 1 | $8.95 | $8.95 | https://www.adafruit.com (https://www.adafruit.com/product/3500) |  | https://www.adafruit
Header Kit for Feather - 12-pin and 16-pin Female Header Set | 2 | 2 | $0.95 | $1.90 | https://www.adafruit.com/product/2886
NeoPixel Diffused 5mm Through-Hole LED - 5 Pack | 2 | 2 | $4.95 | $9.90 | https://www.adafruit.com/product/1938
NeoPixel Jewel - 7 x 5050 RGB LED with Integrated Drivers | 1 | 1 | $5.95 | $5.95 | https://www.adafruit.com/product/2226
NeoPixel Stick - 8 x 5050 RGBW LEDs - Warm White - ~3000K | 2 | 2 | $7.95 | $15.90 | https://www.adafruit.com/product/2867
 |  |  |  | $140.35
AMAZON
12v Lithium Battery | 1 |  | $112.99 | $0.00 | https://www.amazon.com (https://www.amazon.com/gp/product/B00JK06CK8/ref=ppx_yo_dt_b_search_asin_title?ie=UTF8&psc=1) |  | https://www.amazon.c
12v Stronger Amperage | 1 |  | $60.00 | $0.00 | https://www.ebay.com (https://www.ebay.com/itm/313551938183?hash=item490126e287:g:gzQAAOSwZ6tfSGYj)
24v Lithium Battery (24V 28ah electric bicycle Li-ion battery 500W) | 1 | 1 | $100.00 | $100.00 | https://www.ebay.com (https://www.ebay.com/itm/373419267114?hash=item56f185d42a:g:5cYAAOSwmCxfzxCO)
300MM lazy susan | 1 | 1 | $25.00 | $25.00 | https://www.amazon.com/gp/product/B01L8EHD6K/ref=ppx_yo_dt_b_search_asin_title?ie=UTF8&psc=1 |  | https://www.amazon.c
608zz | 4 | 1 | $9.79 | $9.79 | https://www.amazon.com (https://www.amazon.com/Sackorange-Skateboard-Bearings-Miniature-Bearings%EF%BC%88Pack/dp/B07216D1SZ) |  | https://www.amazon.c
Amp | 1 | 1 | $16.99 | $16.99 | https://www.amazon.com (https://www.amazon.com/gp/product/B01N1UHTU1/ref=ppx_yo_dt_b_search_asin_title?ie=UTF8&psc=1) |  | https://www.amazon.c
power distribution and fuse system | 1 | 1 | $15.99 | $15.99 | SOYOND Waterproof Fuse Block,fuse Box With Led Indicator Damp-proof Cover 12 Circuits With Negative Marine Fuse Block For Dc 12/24v Automotive Car Marine Boat RV Truck https://www.amazon.com/dp/B07HDZVW3P
Fuse block | 1 | 0 | $9.99 | $0.00 | https://www.amazon.com (https://www.amazon.com/WATERWICH-Standard-Circuit-Waterproof-Protection/dp/B07CWNTJL5) |  | https://www.amazon.c
Fuse block 12v 6-way | 1 | 1 | $13.99 | $13.99 | https://www.amazon.com/gp/product/B07HDZVW3P/ref=ppx_yo_dt_b_search_asin_title?ie=UTF8&psc=1 |  | https://www.amazon.c
Micro to A adapter | 1 | 1 | $4.96 | $4.96 | https://www.amazon.com/Rankie-Female-Adapter-Convertor-3-Pack/dp/B00YOX4JU6 |  | https://www.amazon.c
Pot (200k) | 1 | 1 | $7.42 | $7.42 | https://www.amazon.com/Uxcell-a15011600ux0235-Linear-Rotary-Potentiometer/dp/B01DKCUVMQ |  | https://www.amazon.c
Power Remote On/Off Controller | 1 | 1 | $23.00 | $23.00 | https://www.amazon.com/dp/B07P4DZ2JT |  | https://www.amazon.c
Power Switch (Optional) | 1 | 1 | $5.55 | $5.55 | https://www.amazon.com/Gardner-Bender-GSW-10-Electrical-Terminal/dp/B000HOT1CM?pid=Q1gG8Eh&s=industrial |  | https://www.amazon.c
Servos (BB Series) | 2 | 2 | $42.99 | $85.98 | https://www.amazon.com/PDI-HV2060MG-Voltage-Digital-Helicopter-Airplane/dp/B07PSLD9P9 |  | https://www.amazon.c
Slipring | 2 | 2 | $17.71 | $35.42 | https://www.amazon.com/Taidacent-Conductive-Collector-Electrical-Commutator/dp/B07NW9PT4P |  | https://www.amazon.c
Small Buck | 1 | 1 | $11.99 | $11.99 | https://www.amazon.com/gp/product/B07CVBG8CT/ref=ppx_yo_dt_b_search_asin_title?ie=UTF8&psc=1 |  | https://www.amazon.c
Voltage Sensor | 1 | 1 | $5.39 | $5.39 | https://www.amazon.com/HiLetgo-Voltage-Detection-Arduino-Electronic/dp/B01HTC4XKY?s=hi |  | https://www.amazon.c
Worm gear motor (130rpm) (S2S) | 1 | 1 | $26.76 | $26.76 | https://www.amazon.com/gp/product/B08KFX6XG8/ref=ewc_pr_img_1?smid=A2K5DI8VX12AN1&th=1 |  | #REF!
Worm gear motor (65rpm) (S2S) | 1 | 0 | $29.29 | $0.00 | https://www.amazon.com/gp/product/B07KLMM49K/ref=ppx_yo_dt_b_search_asin_title?ie=UTF8&psc=1 |  | https://www.amazon.c
Transducers | 2 | 2 | $24.17 | $48.34 | https://amzn.to/3qkbLBZ
1" 3.5mm headphone cable (right angle) | 1 | 1 | $5.99 | $5.99 | https://amzn.to/3swwPqX
3.5 mm groud loop isolator | 1 | 1 | $11.99 | $11.99 | https://amzn.to/2LSiDrh
Female Pin Headers | 1 | 1 | $5.60 | $5.60 | https://www.amazon.com/dp/B01DLX6RSQ/ref=cm_sw_r_cp_api_glt_fabc_ina53cGbVKJT0JX
15 Sets JST XH 2.54MM 4 PIN Female Single Connector with 300mm Wire 1007 26AWG | 1 | 1 | $8.99 | $8.99 | https://www.amazon.com/2-54MM-Female-Single-Connector-300mm/dp/B01IZAHR5M?s=electronics
20 PCS 3 PIN JST XH Female Connector on One Side - 200mm 1007 26 AWG & 20 PCS 3 PIN JST XH Male Connector | 1 | 1 | $7.99 | $7.99 | https://www.amazon.com/2-54MM-Female-Single-Connector-Wires/dp/B07FBHKY8G?s=electronics
30 PCS 2 PIN JST XH Female Connector on Both Side - 200mm 1007 26 AWG & 60 PCS 2 PIN JST XH Male Connector | 1 | 1 | $7.99 | $7.99 | https://www.amazon.com/LATTECH-Female-Connector-Electric-Length/dp/B07NTY4972?s=electronics
50cm Female to Female dupont | 1 | 1 | $5.00 | $5.00 | Amazon.com: EDGELEC 120pcs 10cm Dupont Wire Female to Female Breadboard Jumper Wires 3.9 inch 1pin-1pin 2.54mm Connector Multicolored Ribbon Cables DIY Wires Length 10 15 20 30 40 50 100cm Optional: Home Audio & Theater (https://www.amazon.com/EDGELEC-Breadboard-1pin-1pin-Connector-Multicolored/dp/B07GCZBH51)
 |  |  |  | $490.12
ANDYMARK
NeveRest Classic 60 Gearmotor | 1 | 1 | $31.50 | $31.50 | https://www.andymark.com/products/neverest-classic-60-gearmotor?quantity=1 |  | https://www.andymark
JST-PH ENC Cable to breakouts | 1 | 1 | $5.00 | $5.00 | https://www.andymark.com/products/hall-effect-encoder-cable-encoder-connector-to-split-end-connector
DF ROBOT
Motor Driver 12A | 2 | 2 | $29.00 | $58.00 | https://www.dfrobot.com/product-1861.html |  | https://www.dfrobot.
DFRDuino Player (i2C) MP3 playerwiki.dfrobot.com/DFRduino_Player__SKU_DFR0112_ | 1 | 1 | $9.00 | $9.00 | DFPlayer Pro MP3 Player Module for Voice Activated System | Arduino / Raspberry Pi - DFRobot (https://www.dfrobot.com/product-2232.html)
DF Payer Mini
MCMASTER CARR
#4 screw x .5” (100pk) | 6 | 1 | $2.40 | $2.40 | https://www.mcmaster.com/90190A108 |  | https://www.mcmaster
#4 screw x .75” (100pk) | 8 | 1 | $2.94 | $2.94 | https://www.mcmaster.com/90190A113 |  | https://www.mcmaster
#4 screw 1/4" long (100pk) | 25 | 1 | $2.19 | $2.19 | https://www.mcmaster.com/90190A106/ |  | https://www.mcmaster
#6 washers (100pk) | 100 | 1 | $1.20 | $1.20 | https://www.mcmaster.com/92141A008 |  | https://www.mcmaster
#10 nuts (100pk) | 2 | 1 | $3.77 | $3.77 | https://www.mcmaster.com/91841A195 |  | https://www.mcmaster
#10 rod ends (RH Thread) | 4 | 4 | $3.77 | $15.08 | https://www.mcmaster.com/60645K31 |  | https://www.mcmaster
#10 threaded rod (will cut to length) | 1 | 1 | $1.14 | $1.14 | https://www.mcmaster.com/90032A048 |  | https://www.mcmaster
#10 x 2” | 1 | 1 | $2.65 | $2.65 | https://www.mcmaster.com/92949A275 |  | https://www.mcmaster
1/4"-20 x 1” (50pk) | 8 | 1 | $8.49 | $8.49 | https://www.mcmaster.com/92949A542 |  | https://www.mcmaster
1/4”-20 x 7/16” (50pk) | 4 | 1 | $6.03 | $6.03 | https://www.mcmaster.com/92949A833 |  | https://www.mcmaster
6-32 x .375” (100pk) | 4 | 1 | $3.72 | $3.72 | https://www.mcmaster.com/92949A146 |  | https://www.mcmaster
6-32 x .5” (100pk) | 4 | 1 | $3.72 | $3.72 | https://www.mcmaster.com/92949A148 |  | https://www.mcmaster
6-32 x .75” (100pk) | 4 | 1 | $4.41 | $4.41 | https://www.mcmaster.com/92949A151 |  | https://www.mcmaster
6-32 x 1” (100pk) | 12 | 1 | $5.42 | $5.42 | https://www.mcmaster.com/92949A153 |  | https://www.mcmaster
10-32 square nuts (100pk) | 8 | 1 | $3.39 | $3.39 | https://www.mcmaster.com/94855A283 |  | https://www.mcmaster
10-32 x 1.25” FH (25pk) | 4 | 1 | $5.02 | $5.02 | https://www.mcmaster.com/91253A012 |  | https://www.mcmaster
10-32 x 2” flat head (10pk) | 6 | 1 | $6.21 | $6.21 | https://www.mcmaster.com/90585A299 |  | https://www.mcmaster
M3 lock nut (100pk) | 4 | 1 | $3.57 | $3.57 | https://www.mcmaster.com/90576A102 |  | https://www.mcmaster
M3 x 10 (100 pk) | 11 | 1 | $8.38 | $8.38 | https://www.mcmaster.com/92095A182 |  | https://www.mcmaster
M3 x 25mm (50pk) | 1 | 1 | $6.13 | $6.13 | https://www.mcmaster.com/92095A186 |  | https://www.mcmaster
M4 nut (100 pk) | 2 | 1 | $1.41 | $1.41 | https://www.mcmaster.com/90592A090 |  | https://www.mcmaster
M4 x 45mm (25pk) | 2 | 1 | $6.81 | $6.81 | https://www.mcmaster.com/92095A205 |  | https://www.mcmaster
M5 flange nut (100pk) | 14 | 1 | $10.02 | $10.02 | https://www.mcmaster.com/97400A858 |  | https://www.mcmaster
M5 x 35mm Flat Head (25pk) | 12 | 1 | $7.22 | $7.22 | https://www.mcmaster.com/92125A222 |  | https://www.mcmaster
M5 x 55 Flat Head (25pk) | 2 | 1 | $9.63 | $9.63 | https://www.mcmaster.com/92125A218 |  | https://www.mcmaster
M8 lock nut (50pk) | 2 | 1 | $7.86 | $7.86 | https://www.mcmaster.com/97131A140 |  | https://www.mcmaster
M8 x 50mm (25pk) | 1 | 1 | $9.14 | $9.14 | https://www.mcmaster.com/91280A546 |  | https://www.mcmaster
M8 x 55mm (25pk) | 1 | 1 | $8.91 | $8.91 | https://www.mcmaster.com/91280A548 |  | https://www.mcmaster
 |  |  |  | $156.86
SERVOCITY
0.375" to 6mm Set Screw Shaft Coupler | 1 | 1 | $4.99 | $4.99 | https://www.servocity.com/0-375-to-6mm-set-screw-shaft-coupler/ |  | https://www.servocit
1” HD Hub | 3 | 3 | $14.99 | $44.97 | https://www.servocity.com/1-bore-face-tapped-heavy-duty-clamping-hub-1-50-pattern/ |  | https://www.servocit
1” ID bearing | 8 | 8 | $9.99 | $79.92 | https://www.servocity.com/1-id-x-1-245-od-flanged-ball-bearing/ |  | https://www.servocit
1” stainless tube cut to 6.75” | 2 | 2 | $8.69 | $17.38 | https://www.servocity.com/1-00-x-8-00-stainless-steel-tubing/ |  | https://www.servocit
118rpm motor (drive) | 1 | 1 | $39.99 | $39.99 | https://www.servocity.com/118-rpm-hd-premium-planetary-gear-motor/ |  | https://www.servocit
1621rpm motor (FlyWheel) | 1 | 1 | $39.99 | $39.99 | https://www.servocity.com/1-621-rpm-hd-premium-planetary-gear-motor/ |  | https://www.servocit
16t sprocket | 1 | 1 | $3.99 | $3.99 | https://www.servocity.com/16-tooth-0-770-aluminum-hub-mount-sprocket-0-250-pitch/ |  | https://www.servocit
3/8" alu, tube | 1 | 1 | $4.09 | $4.09 | https://www.servocity.com/0-375-3-8-x-12-00-aluminum-tubing/ |  | https://www.servocit
3/8" bore clamp | 1 | 1 | $6.99 | $6.99 | https://www.servocity.com/0-375-0-770-clamping-hub/ |  | https://www.servocit
3/8" ID x 5/8" OD Non-Flanged Ball Bearing (2pk) | 4 | 2 | $2.79 | $5.58 | https://www.servocity.com/3-8-id-x-5-8-od-non-flanged-ball-bearing-2-pack/ |  | https://www.servocit
Alternative via Active Robots website (UK) | 2 | 1 | $16.00 | $16.00 | https://www.active-robots.com/1-4-id-x-1-2-od-non-flanged-ball-bearing-2-pack.html
32mm clamp | 4 | 4 | $6.99 | $27.96 | https://www.servocity.com/32mm-bore-bottom-tapped-clamping-mount/ |  | https://www.servocit
40t sprocket | 1 | 1 | $6.39 | $6.39 | https://www.servocity.com/40-tooth-1-50-aluminum-hub-mount-sprockets-0-250-pitch/ |  | https://www.servocit
6mm d hub | 2 | 2 | $6.99 | $13.98 | https://www.servocity.com/1311-series-thru-hole-sonic-hub-6mm-d-bore/ |  | https://www.servocit
8mm hub | 1 | 1 | $5.99 | $5.99 | https://www.servocity.com/1309-series-sonic-hub-8mm-bore/ |  | https://www.servocit
Chain | 1 | 1 | $5.99 | $5.99 | https://www.servocity.com/0-250-chain-5-feet/ |  | https://www.servocit
Chain Tool (breaker) | 1 | 1 | $25.00 | $25.00 | https://www.servocity.com/0-250-pitch-chain-tool/
 |  |  |  | $349.20 |  |  | https://www.servocit
SPARKFUN Electronics
SparkFun Qwiic MP3 Trigger | 0 | 0 | $20.00 | $0.00 | https://www.sparkfun.com/products/19030
 | 1 | 1 | $56.50 | $56.50 | LilyPad MP3 - SparkFun Electronics (https://www.sparkfun.com/lilypad-mp3.html)
Qwiic Cable - Grove Adapter (100mm) | 1 | 1 | $1.50 | $1.50 | https://www.sparkfun.com/products/15109
 |  |  |  | $58.00 |  |  | https://www.servocit
POLOLU Robotics and Electronics
Screw Terminal Block: 2-Pin, 5 mm Pitch | 3 | 1 | $1.50 | $1.50 | https://www.pololu.com/product/2440
5V, 3.2A Step-Down Voltage Regulator D36V28F5 | 1 | 1 | $11.95 | $11.95 | https://www.pololu.com/product/3782
6V, 2.7A Step-Down Voltage Regulator D36V28F6 | 1 | 1 | $11.95 | $11.95 | https://www.pololu.com/product/3783
9V, 2.6A Step-Down Voltage Regulator D36V28F9 | 1 | 1 | $11.95 | $11.95 | https://www.pololu.com/product/3785
(2.54 mm) Female Header: 2x5-Pin, Straight | 1 | 1 | 0.69 | $0.69 | https://www.pololu.com/product/1025
(2.54 mm) Female Header: 1x5-Pin, Straight | 2 | 2 | 0.44 | $0.88 | https://www.pololu.com/product/1015
(2.54 mm) Female Header: 1x5-Pin, Straight | 2 | 2 | 0.44 | $0.88 | https://www.pololu.com/product/1015
 |  |  |  | $39.80
 |  |  | Total Cost: | $1243.33

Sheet: Build Parts
S2SArm
55 x 4mm bolts
5 x 5mm bolts
.5 x small screws
FlyWheelArm

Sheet: Sheet1
ALTERNATE BOM 2025-2027
Part | Total needed | Purchase | Cost per | Cost total | URL
ADAFRUIT
Adafruit Feather 32u4 Basic Proto | 1 | 1 | $19.95 | $19.95 | https://www.adafruit.com/product/2771
Hall effect Sensor | 1 | 1 | $2.00 | $2.00 | https://www.adafruit.com (https://www.adafruit.com/product/158)
Assembled Adafruit HUZZAH32 – ESP32 Feather Board - with Stacking Headers | 2 | 2 | $21.95 | $43.90 | https://www.adafruit.com (https://www.adafruit.com/product/3619)
MPU | 1 | 1 | $6.95 | $6.95 | https://www.adafruit.com (https://www.adafruit.com/product/3886)
Trinket m0 | 1 | 1 | $8.95 | $8.95 | https://www.adafruit.com (https://www.adafruit.com/product/3500)
Header Kit for Feather - 12-pin and 16-pin Female Header Set | 2 | 2 | $0.95 | $1.90 | https://www.adafruit.com/product/2886
NeoPixel Diffused 5mm Through-Hole LED - 5 Pack | 2 | 2 | $4.95 | $9.90 | https://www.adafruit.com/product/1938
NeoPixel Jewel - 7 x 5050 RGB LED with Integrated Drivers | 1 | 1 | $5.95 | $5.95 | https://www.adafruit.com/product/2226
NeoPixel Stick - 8 x 5050 RGBW LEDs - Warm White - ~3000K | 2 | 2 | $7.95 | $15.90 | https://www.adafruit.com/product/2867
 |  |  |  | $115.40
AMAZON
12v Lithium Battery | 1 |  | $112.99 | $0.00 | https://www.amazon.com (https://www.amazon.com/gp/product/B00JK06CK8/ref=ppx_yo_dt_b_search_asin_title?ie=UTF8&psc=1)
12v Stronger Amperage | 1 |  | $60.00 | $0.00 | https://www.ebay.com (https://www.ebay.com/itm/313551938183?hash=item490126e287:g:gzQAAOSwZ6tfSGYj)
24v Lithium Battery (24V 28ah electric bicycle Li-ion battery 500W) | 1 | 1 | $100.00 | $100.00 | https://www.ebay.com (https://www.ebay.com/itm/373419267114?hash=item56f185d42a:g:5cYAAOSwmCxfzxCO)
300MM lazy susan | 1 | 1 | $25.00 | $25.00 | https://www.amazon.com/gp/product/B01L8EHD6K/ref=ppx_yo_dt_b_search_asin_title?ie=UTF8&psc=1
608zz | 4 | 1 | $9.79 | $9.79 | https://www.amazon.com (https://www.amazon.com/Sackorange-Skateboard-Bearings-Miniature-Bearings%EF%BC%88Pack/dp/B07216D1SZ)
Amp | 1 | 1 | $16.99 | $16.99 | https://www.amazon.com (https://www.amazon.com/gp/product/B01N1UHTU1/ref=ppx_yo_dt_b_search_asin_title?ie=UTF8&psc=1)
power distribution and fuse system | 1 | 1 | $15.99 | $15.99 | SOYOND Waterproof Fuse Block,fuse Box With Led Indicator Damp-proof Cover 12 Circuits With Negative Marine Fuse Block For Dc 12/24v Automotive Car Marine Boat RV Truck https://www.amazon.com/dp/B07HDZVW3P
Fuse block | 1 | 0 | $9.99 | $0.00 | https://www.amazon.com (https://www.amazon.com/WATERWICH-Standard-Circuit-Waterproof-Protection/dp/B07CWNTJL5)
Fuse block 12v 6-way | 1 | 1 | $13.99 | $13.99 | https://www.amazon.com/gp/product/B07HDZVW3P/ref=ppx_yo_dt_b_search_asin_title?ie=UTF8&psc=1
Micro to A adapter | 1 | 1 | $4.96 | $4.96 | https://www.amazon.com/Rankie-Female-Adapter-Convertor-3-Pack/dp/B00YOX4JU6
Pot (200k) | 1 | 1 | $7.42 | $7.42 | https://www.amazon.com/Uxcell-a15011600ux0235-Linear-Rotary-Potentiometer/dp/B01DKCUVMQ
Power Remote On/Off Controller | 1 | 1 | $23.00 | $23.00 | https://www.amazon.com/dp/B07P4DZ2JT
Power Switch (Optional) | 1 | 1 | $5.55 | $5.55 | https://www.amazon.com/Gardner-Bender-GSW-10-Electrical-Terminal/dp/B000HOT1CM?pid=Q1gG8Eh&s=industrial
Servos (BB Series) | 2 | 2 | $42.99 | $85.98 | https://www.amazon.com/PDI-HV2060MG-Voltage-Digital-Helicopter-Airplane/dp/B07PSLD9P9
Slipring | 2 | 2 | $17.71 | $35.42 | https://www.amazon.com/Taidacent-Conductive-Collector-Electrical-Commutator/dp/B07NW9PT4P
Small Buck | 1 | 1 | $11.99 | $11.99 | https://www.amazon.com/gp/product/B07CVBG8CT/ref=ppx_yo_dt_b_search_asin_title?ie=UTF8&psc=1
Voltage Sensor | 1 | 1 | $5.39 | $5.39 | https://www.amazon.com/HiLetgo-Voltage-Detection-Arduino-Electronic/dp/B01HTC4XKY?s=hi
Worm gear motor (130rpm) (S2S) | 1 | 1 | $26.76 | $26.76 | https://www.amazon.com/gp/product/B08KFX6XG8/ref=ewc_pr_img_1?smid=A2K5DI8VX12AN1&th=1
Worm gear motor (65rpm) (S2S) | 1 | 0 | $29.29 | $0.00 | https://www.amazon.com/gp/product/B07KLMM49K/ref=ppx_yo_dt_b_search_asin_title?ie=UTF8&psc=1
Transducers | 2 | 2 | $24.17 | $48.34 | https://amzn.to/3qkbLBZ
1" 3.5mm headphone cable (right angle) | 1 | 1 | $5.99 | $5.99 | https://amzn.to/3swwPqX
3.5 mm groud loop isolator | 1 | 1 | $11.99 | $11.99 | https://amzn.to/2LSiDrh
Female Pin Headers | 1 | 1 | $5.60 | $5.60 | https://www.amazon.com/dp/B01DLX6RSQ/ref=cm_sw_r_cp_api_glt_fabc_ina53cGbVKJT0JX
15 Sets JST XH 2.54MM 4 PIN Female Single Connector with 300mm Wire 1007 26AWG | 1 | 1 | $8.99 | $8.99 | https://www.amazon.com/2-54MM-Female-Single-Connector-300mm/dp/B01IZAHR5M?s=electronics
20 PCS 3 PIN JST XH Female Connector on One Side - 200mm 1007 26 AWG & 20 PCS 3 PIN JST XH Male Connector | 1 | 1 | $7.99 | $7.99 | https://www.amazon.com/2-54MM-Female-Single-Connector-Wires/dp/B07FBHKY8G?s=electronics
30 PCS 2 PIN JST XH Female Connector on Both Side - 200mm 1007 26 AWG & 60 PCS 2 PIN JST XH Male Connector | 1 | 1 | $7.99 | $7.99 | https://www.amazon.com/LATTECH-Female-Connector-Electric-Length/dp/B07NTY4972?s=electronics
50cm Female to Female dupont | 1 | 1 | $5.00 | $5.00 | Amazon.com: EDGELEC 120pcs 10cm Dupont Wire Female to Female Breadboard Jumper Wires 3.9 inch 1pin-1pin 2.54mm Connector Multicolored Ribbon Cables DIY Wires Length 10 15 20 30 40 50 100cm Optional: Home Audio & Theater (https://www.amazon.com/EDGELEC-Breadboard-1pin-1pin-Connector-Multicolored/dp/B07GCZBH51)
 |  |  |  | $490.12
ANDYMARK
NeveRest Classic 60 Gearmotor | 1 | 1 | $31.50 | $31.50 | https://www.andymark.com/products/neverest-classic-60-gearmotor?quantity=1
JST-PH ENC Cable to breakouts | 1 | 1 | $5.00 | $5.00 | https://www.andymark.com/products/hall-effect-encoder-cable-encoder-connector-to-split-end-connector
DF ROBOT
Motor Driver 12A | 2 | 2 | $29.00 | $58.00 | https://www.dfrobot.com/product-1861.html
DFRDuino Player (i2C) MP3 playerwiki.dfrobot.com/DFRduino_Player__SKU_DFR0112_ | 1 | 1 | $9.00 | $9.00 | DFPlayer Pro MP3 Player Module for Voice Activated System | Arduino / Raspberry Pi - DFRobot (https://www.dfrobot.com/product-2232.html)
DF Payer Mini
MCMASTER CARR
#4 screw x .5” (100pk) | 6 | 1 | $2.40 | $2.40 | https://www.mcmaster.com/90190A108
#4 screw x .75” (100pk) | 8 | 1 | $2.94 | $2.94 | https://www.mcmaster.com/90190A113
#4 screw 1/4" long (100pk) | 25 | 1 | $2.19 | $2.19 | https://www.mcmaster.com/90190A106/
#6 washers (100pk) | 100 | 1 | $1.20 | $1.20 | https://www.mcmaster.com/92141A008
#10 nuts (100pk) | 2 | 1 | $3.77 | $3.77 | https://www.mcmaster.com/91841A195
#10 rod ends (RH Thread) | 4 | 4 | $3.77 | $15.08 | https://www.mcmaster.com/60645K31
#10 threaded rod (will cut to length) | 1 | 1 | $1.14 | $1.14 | https://www.mcmaster.com/90032A048
#10 x 2” | 1 | 1 | $2.65 | $2.65 | https://www.mcmaster.com/92949A275
1/4"-20 x 1” (50pk) | 8 | 1 | $8.49 | $8.49 | https://www.mcmaster.com/92949A542
1/4”-20 x 7/16” (50pk) | 4 | 1 | $6.03 | $6.03 | https://www.mcmaster.com/92949A833
6-32 x .375” (100pk) | 4 | 1 | $3.72 | $3.72 | https://www.mcmaster.com/92949A146
6-32 x .5” (100pk) | 4 | 1 | $3.72 | $3.72 | https://www.mcmaster.com/92949A148
6-32 x .75” (100pk) | 4 | 1 | $4.41 | $4.41 | https://www.mcmaster.com/92949A151
6-32 x 1” (100pk) | 12 | 1 | $5.42 | $5.42 | https://www.mcmaster.com/92949A153
10-32 square nuts (100pk) | 8 | 1 | $3.39 | $3.39 | https://www.mcmaster.com/94855A283
10-32 x 1.25” FH (25pk) | 4 | 1 | $5.02 | $5.02 | https://www.mcmaster.com/91253A012
10-32 x 2” flat head (10pk) | 6 | 1 | $6.21 | $6.21 | https://www.mcmaster.com/90585A299
M3 lock nut (100pk) | 4 | 1 | $3.57 | $3.57 | https://www.mcmaster.com/90576A102
M3 x 10 (100 pk) | 11 | 1 | $8.38 | $8.38 | https://www.mcmaster.com/92095A182
M3 x 25mm (50pk) | 1 | 1 | $6.13 | $6.13 | https://www.mcmaster.com/92095A186
M4 nut (100 pk) | 2 | 1 | $1.41 | $1.41 | https://www.mcmaster.com/90592A090
M4 x 45mm (25pk) | 2 | 1 | $6.81 | $6.81 | https://www.mcmaster.com/92095A205
M5 flange nut (100pk) | 14 | 1 | $10.02 | $10.02 | https://www.mcmaster.com/97400A858
M5 x 35mm Flat Head (25pk) | 12 | 1 | $7.22 | $7.22 | https://www.mcmaster.com/92125A222
M5 x 55 Flat Head (25pk) | 2 | 1 | $9.63 | $9.63 | https://www.mcmaster.com/92125A218
M8 lock nut (50pk) | 2 | 1 | $7.86 | $7.86 | https://www.mcmaster.com/97131A140
M8 x 50mm (25pk) | 1 | 1 | $9.14 | $9.14 | https://www.mcmaster.com/91280A546
M8 x 55mm (25pk) | 1 | 1 | $8.91 | $8.91 | https://www.mcmaster.com/91280A548
 |  |  |  | $156.86
SERVOCITY
0.375" to 6mm Set Screw Shaft Coupler | 0 | 0 | $4.99 | $0.00 | https://www.servocity.com/0-375-to-6mm-set-screw-shaft-coupler/
1” HD Hub | 3 | 3 | $7.99 | $23.97 | https://www.servocity.com/1-bore-face-tapped-heavy-duty-clamping-hub-1-50-pattern/
1” HD Hub 1302 | 3 | 3 | $14.99 | $44.97 | https://www.servocity.com/1302-series-clamping-hub-1-bore/
1” ID bearing | 8 | 8 | $9.99 | $79.92 | https://www.servocity.com/1-id-x-1-245-od-flanged-ball-bearing/
1” stainless tube cut to 6.75” | 2 | 2 | $8.69 | $17.38 | https://www.servocity.com/1-00-x-8-00-stainless-steel-tubing/
118rpm motor (drive) | 1 | 1 | $39.99 | $39.99 | https://www.servocity.com/118-rpm-hd-premium-planetary-gear-motor/
1621rpm motor (FlyWheel) | 1 | 1 | $39.99 | $39.99 | https://www.servocity.com/1-621-rpm-hd-premium-planetary-gear-motor/
3307 Series 8mm Pitch Steel Set-Screw Sprocket | 1 | 1 | $9.99 | $9.99 | https://www.servocity.com/3307-series-8mm-pitch-steel-set-screw-sprocket-6mm-d-bore-10-tooth/
3/8" alu, tube | 1 | 1 | $4.09 | $4.09 | https://www.servocity.com/0-375-3-8-x-12-00-aluminum-tubing/
3/8" bore clamp | 1 | 1 | $6.99 | $6.99 | https://www.servocity.com/0-375-0-770-clamping-hub/
3/8" ID x 5/8" OD Non-Flanged Ball Bearing (2pk) | 4 | 2 | $2.79 | $5.58 | https://www.servocity.com/3-8-id-x-5-8-od-non-flanged-ball-bearing-2-pack/
Alternative via Active Robots website (UK) | 2 | 1 | $16.00 | $16.00 | https://www.active-robots.com/1-4-id-x-1-2-od-non-flanged-ball-bearing-2-pack.html
32mm clamp | 0 | 0 | $6.99 | $0.00 | https://www.servocity.com/32mm-bore-bottom-tapped-clamping-mount/
 | 4 | 4 | $8.99 | $35.96 | 1400 Series 1-Side, 2-Post Clamping Mount (32mm Bore) - ServoCity® (https://www.servocity.com/1400-series-1-side-2-post-clamping-mount-32mm-bore/)
Main Drive sprocket 32mm Bore, 28 Tooth | 1 | 0 | $6.39 | $0.00 | https://www.servocity.com/40-tooth-1-50-aluminum-hub-mount-sprockets-0-250-pitch/
Main Drive sprocket 32mm Bore, 42 Tooth | 1 | 1 | $12.99 | $12.99 | https://www.servocity.com/3310-series-8mm-pitch-aluminum-hub-mount-sprocket-32mm-bore-42-tooth/
6mm d hub | 2 | 2 | $6.99 | $13.98 | https://www.servocity.com/1311-series-thru-hole-sonic-hub-6mm-d-bore/
8mm hub | 1 | 1 | $5.99 | $5.99 | https://www.servocity.com/1309-series-sonic-hub-8mm-bore/
Chain 3309 Series 8mm Pitch Plastic Chain | 1 | 1 | $7.99 | $7.99 | https://www.servocity.com/3309-series-8mm-pitch-plastic-chain-50-links-400mm-black/
Chain Tool (breaker) | 1 | 1 | $25.00 | $25.00 | https://www.servocity.com/0-250-pitch-chain-tool/
 |  |  |  | $390.78
SPARKFUN Electronics
SparkFun Qwiic MP3 Trigger | 0 | 0 | $20.00 | $0.00 | https://www.sparkfun.com/products/19030

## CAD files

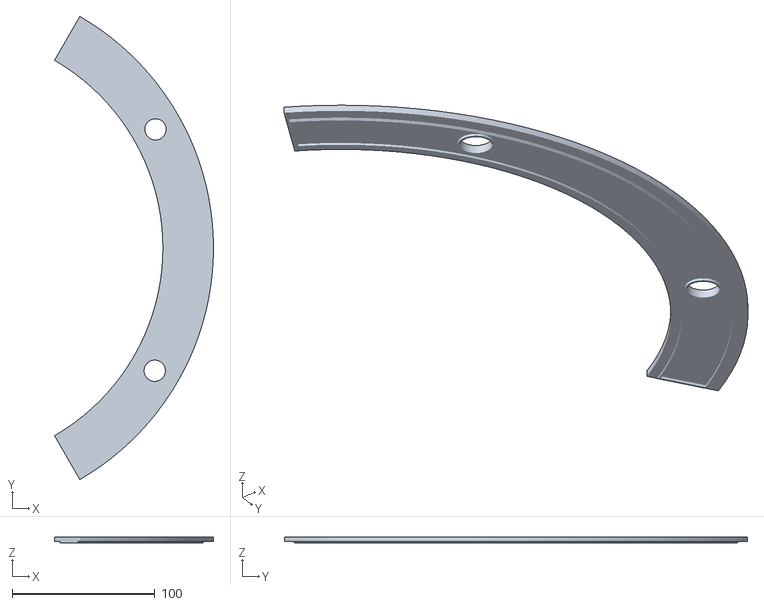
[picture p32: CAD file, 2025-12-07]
STLs/MainSliceCover.stl
111.5 x 324.8 x 4.00

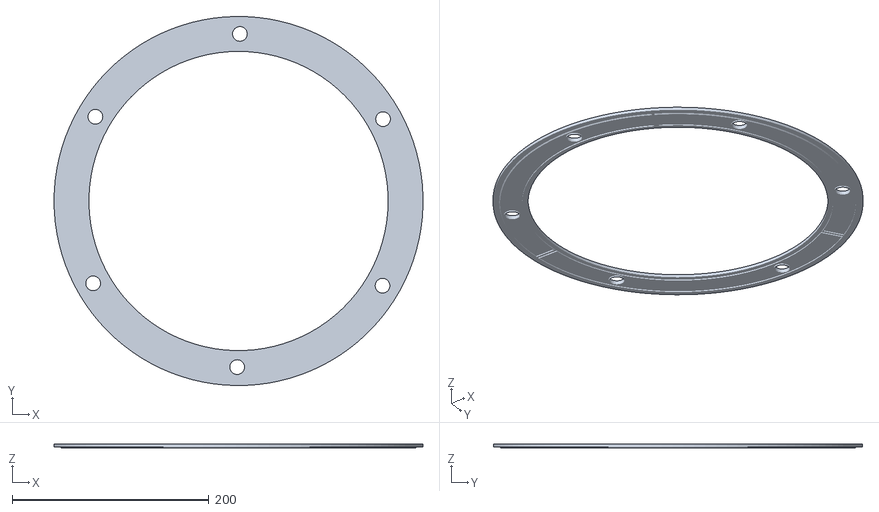
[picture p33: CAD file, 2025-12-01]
STLs/FullBalastCover.stl
374.9 x 375.0 x 4.00

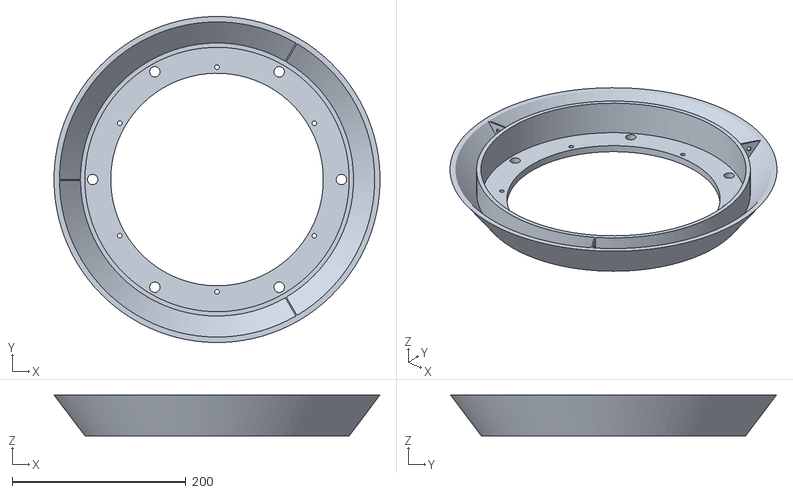
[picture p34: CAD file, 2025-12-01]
STLs/FullBallast.stl
374.9 x 375.0 x 47.0

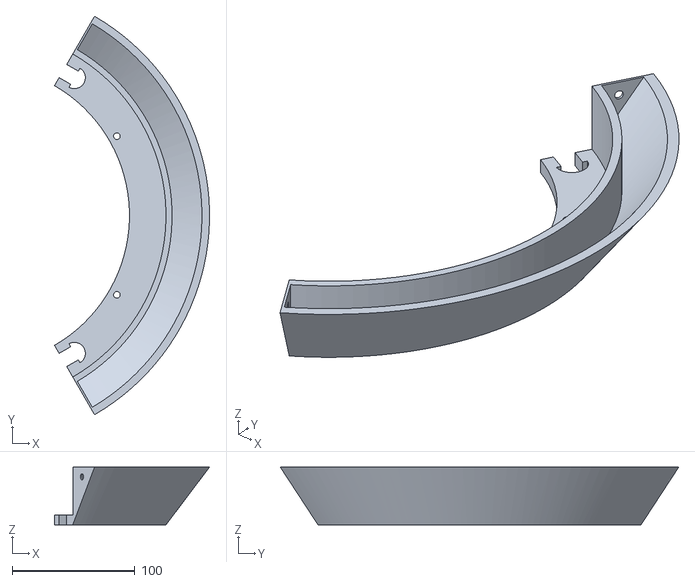
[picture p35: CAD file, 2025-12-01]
STLs/MainSlice.stl
126.3 x 324.8 x 47.0

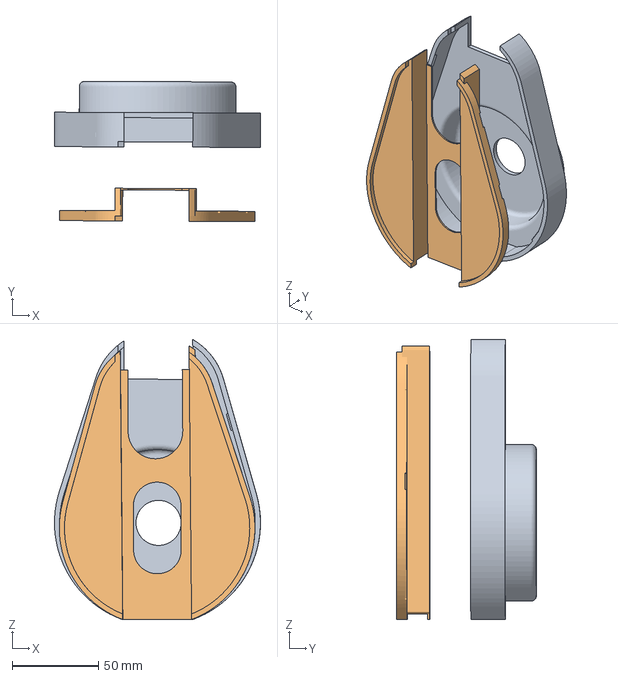
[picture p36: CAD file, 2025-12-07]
STLs/DriveSystem_Gear/OutsideGearCasing.3mf
119.7 x 81.5 x 162.6 mm
OutsideGearCasing.stl
InsideGearCasing.stl

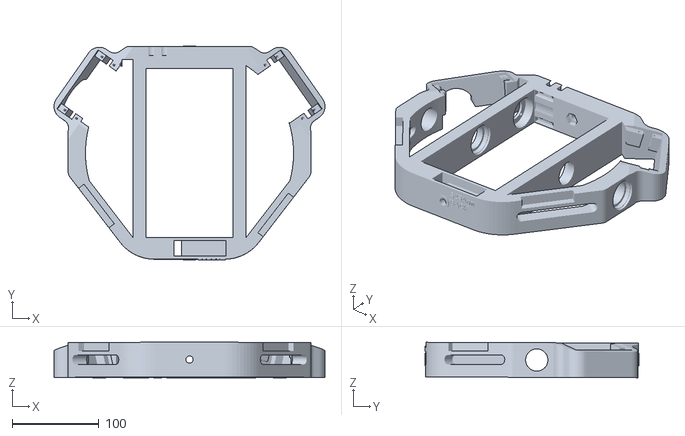
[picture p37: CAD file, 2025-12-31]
STLs/Gantry_140000320032_V2.stl
312.5 x 247.1 x 41.0

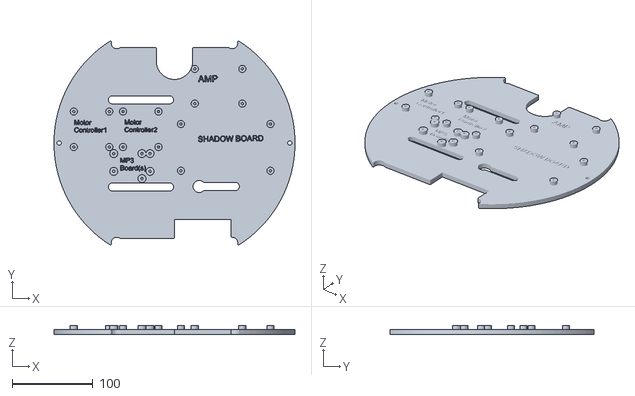
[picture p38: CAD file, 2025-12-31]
STLs/BatteryHarness Cover.stl
298.9 x 253.1 x 11.0

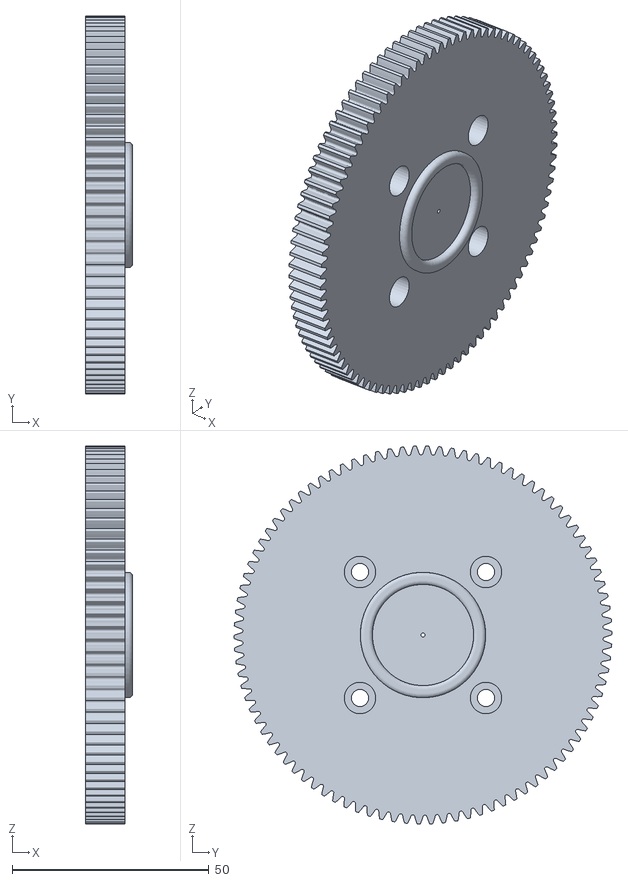
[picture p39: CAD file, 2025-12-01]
STLs/DriveSystem_Gear/Drive Gear (94 teeth) 1302HUB.stl
12.0 x 96.0 x 96.0

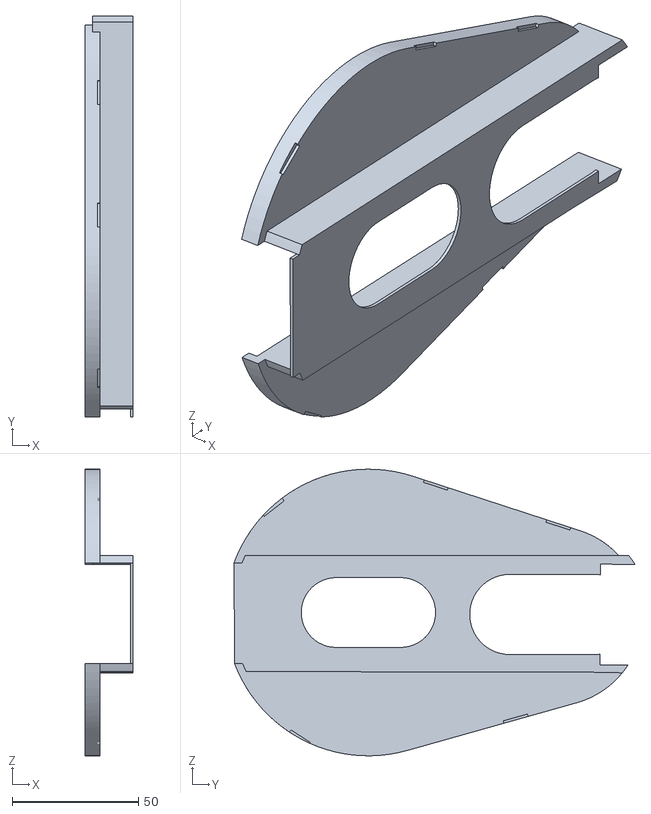
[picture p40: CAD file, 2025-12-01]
STLs/DriveSystem_Gear/InsideGearCasing.stl
19.0 x 158.9 x 113.6

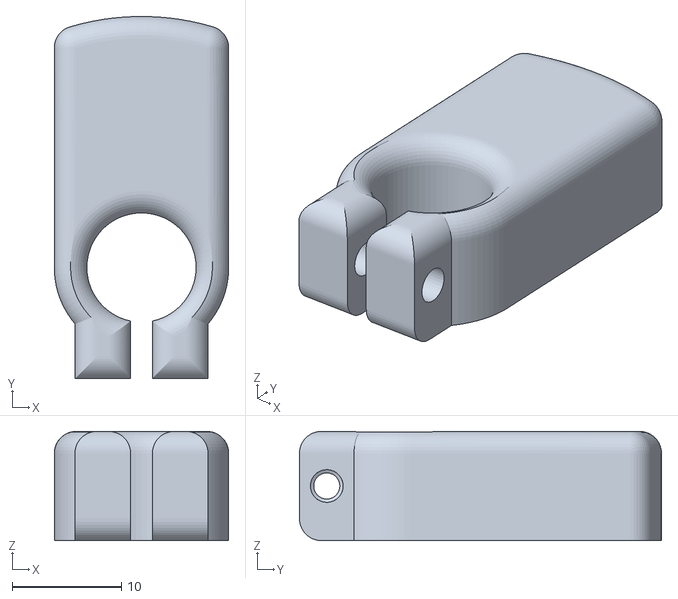
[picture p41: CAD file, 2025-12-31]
STLs/HeadTiltMastHall_10x5rd_12x5sq_V2.stl
16.0 x 33.2 x 10.0

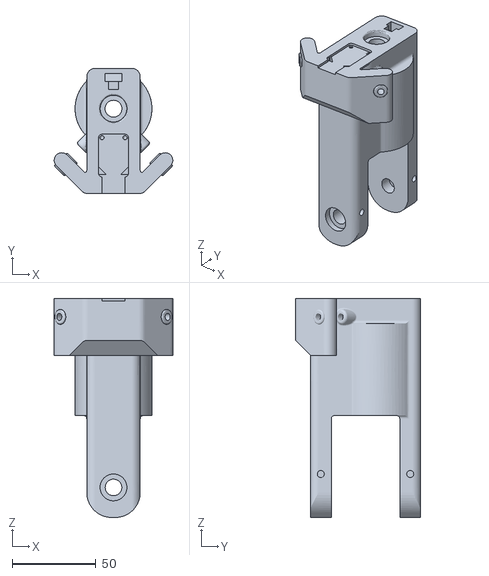
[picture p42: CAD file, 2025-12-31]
STLs/HeadTiltMast_DRV5032_v2.stl
71.0 x 75.0 x 131.0

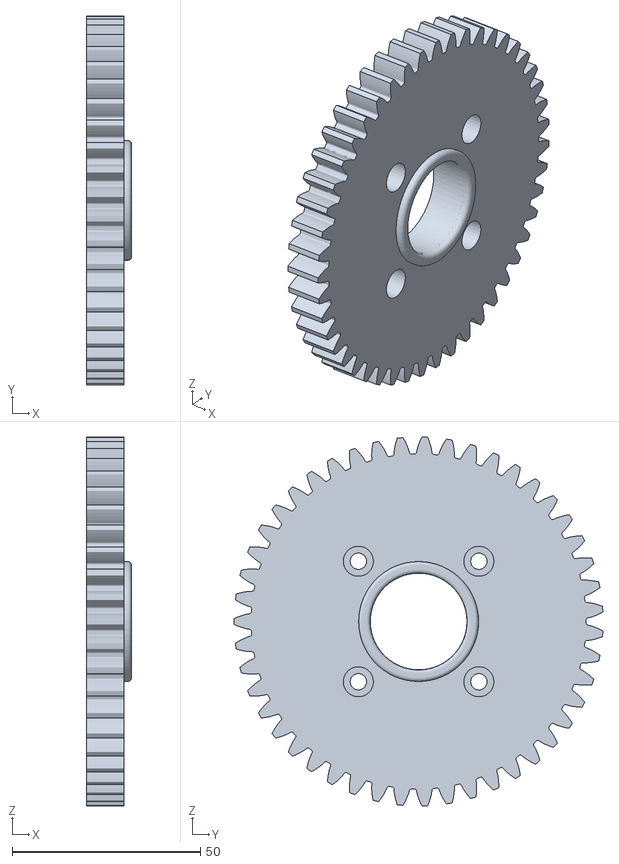
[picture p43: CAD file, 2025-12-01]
STLs/DriveSystem_Gear/Drive Gear (47 teeth) 1302HUB.stl
12.0 x 97.9 x 98.0

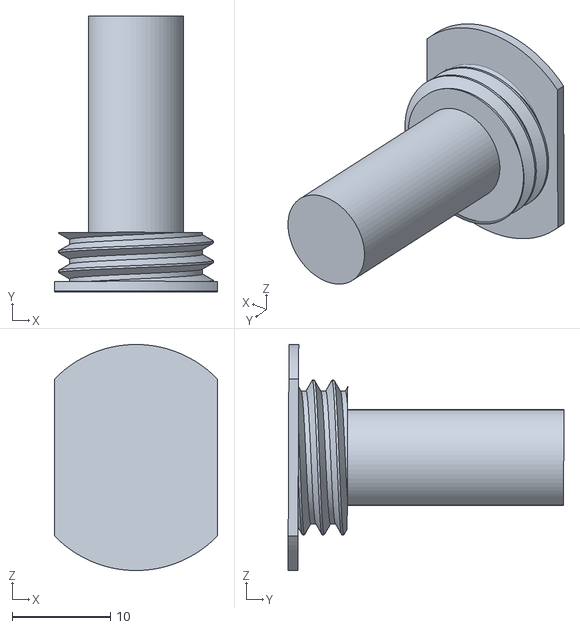
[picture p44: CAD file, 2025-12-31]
STLs/CouplerPin_v2.stl
16.6 x 28.1 x 23.0

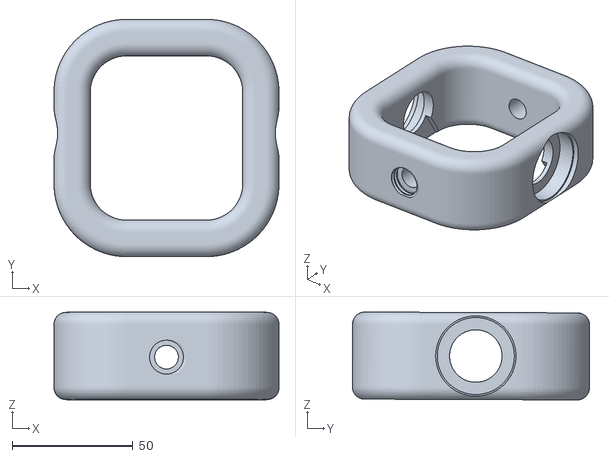
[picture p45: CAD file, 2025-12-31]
STLs/HeadTiltCoupler.stl
93.0 x 98.1 x 36.3

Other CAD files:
STLs/Speakers.stl
STLs/S2SGear_LargeGear.stl
STLs/S2SGear_SmallGear(NEWHUB).stl
STLs/HeadTiltCouplerPin_x2.stl
STLs/BatteryHarness.stl
STLs/CouplerPin.stl
STLs/CouplerScrew_v2.stl
STLs/DriveSystem_Gear/Drive Gear (47 teeth) LEGACY.stl
STLs/DriveSystem_Gear/Drive Gear (94 teeth) LEGACY.stl
STLs/DriveSystem_Gear/Motor Gear (26 teeth) LEGACY.stl
STLs/DriveSystem_Gear/OutsideGearCasing.stl
STLs/FlyWheelArm.stl
STLs/FlyWheelLargeGear.stl
STLs/FlyWheelSmallGear.stl
STLs/Gantry Gear (53 teeth).stl
STLs/Gantry.stl
STLs/HeadTiltMastHall.stl
STLs/HeadTiltMast_Hall_QuicSensor.stl
STLs/HeadTiltMotorCoupler.stl
STLs/Key1.stl
STLs/Pot Gear (50 teeth).stl
STLs/S2SArm.stl
STLs/S2SGear_SmallGear(LEGACY).stl
STLs/S2SGear_SmallGear.stl

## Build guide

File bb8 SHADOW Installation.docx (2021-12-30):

# Arduino IDE Setup

The first thing you will need to do is to download the latest release of the Arduino IDE. You will need to be using version 1.8 or higher for this guide

Arduino IDE Download (http://www.arduino.cc/en/Main/Software)

After you have downloaded and installed the latest version of Arduino IDE, you will need to start the IDE and navigate to the Preferences menu. You can access it from the File menu in Windows or Linux, or the Arduino menu on OS X.

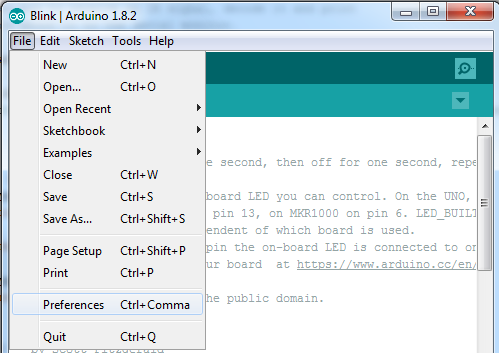
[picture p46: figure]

A dialog will pop up just like the one shown below.

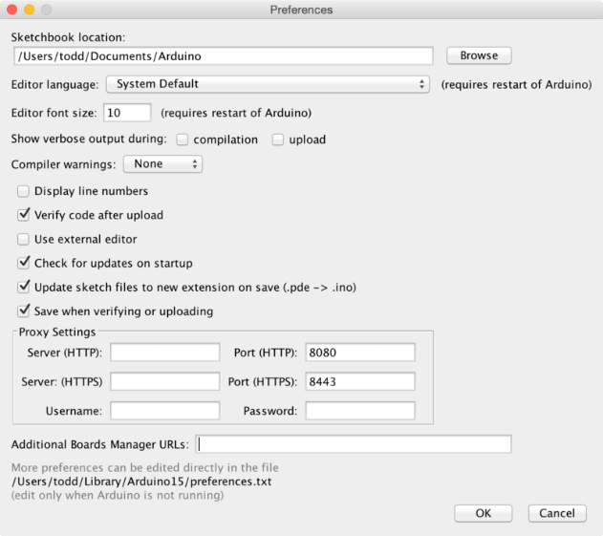
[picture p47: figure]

We will be adding a URL to the new Additional Boards Manager URLs option. The list of URLs is comma separated, and you will only have to add each URL once. New Adafruit boards and updates to existing boards will automatically be picked up by the Board Manager each time it is opened. The URLs point to index files that the Board Manager uses to build the list of available & installed boards.

To find the most up to date list of URLs you can add, you can visit the list of third party board URLs on the Arduino IDE wiki (https://github.com/arduino/Arduino/wiki/Unofficial-list-of-3rd-party-boards-support-urls). We will only need to add one URL to the IDE in this example, but you can add multiple URLS by separating them with commas.

# Adding Adafruit Feather Boards

Copy and paste the link below into the Additional Boards Manager URLs option in the Arduino IDE preferences.

https://adafruit.github.io/arduino-board-index/package_adafruit_index.json

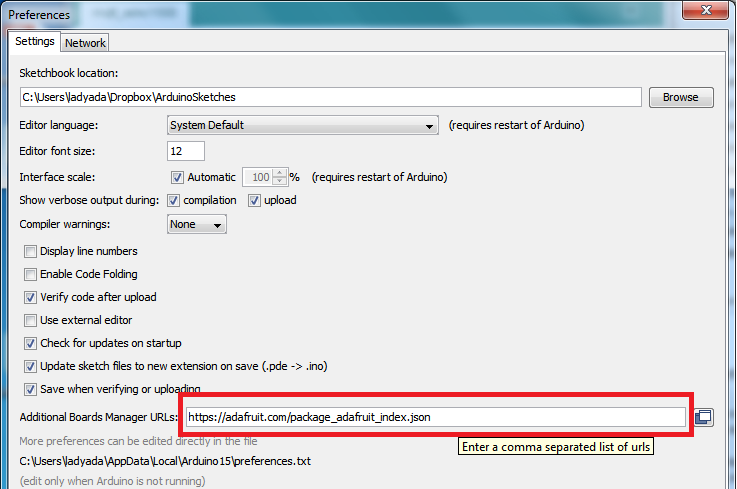
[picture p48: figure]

Here's a short description of each of the Adafruit supplied packages that will be available in the Board Manager when you add the URL:

- Adafruit AVR Boards - Includes support for Flora, Gemma, Feather 32u4, Trinket, & Trinket Pro.

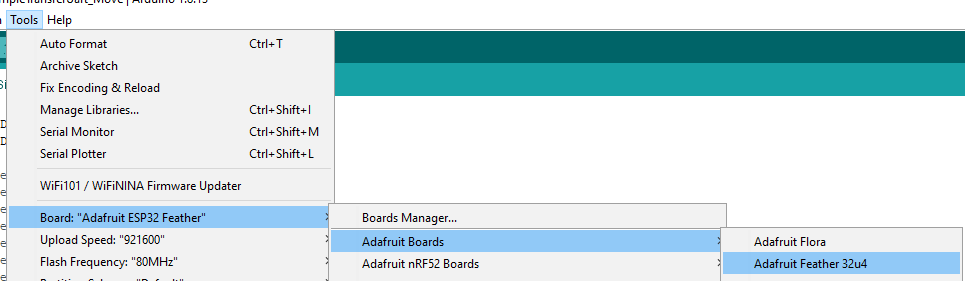
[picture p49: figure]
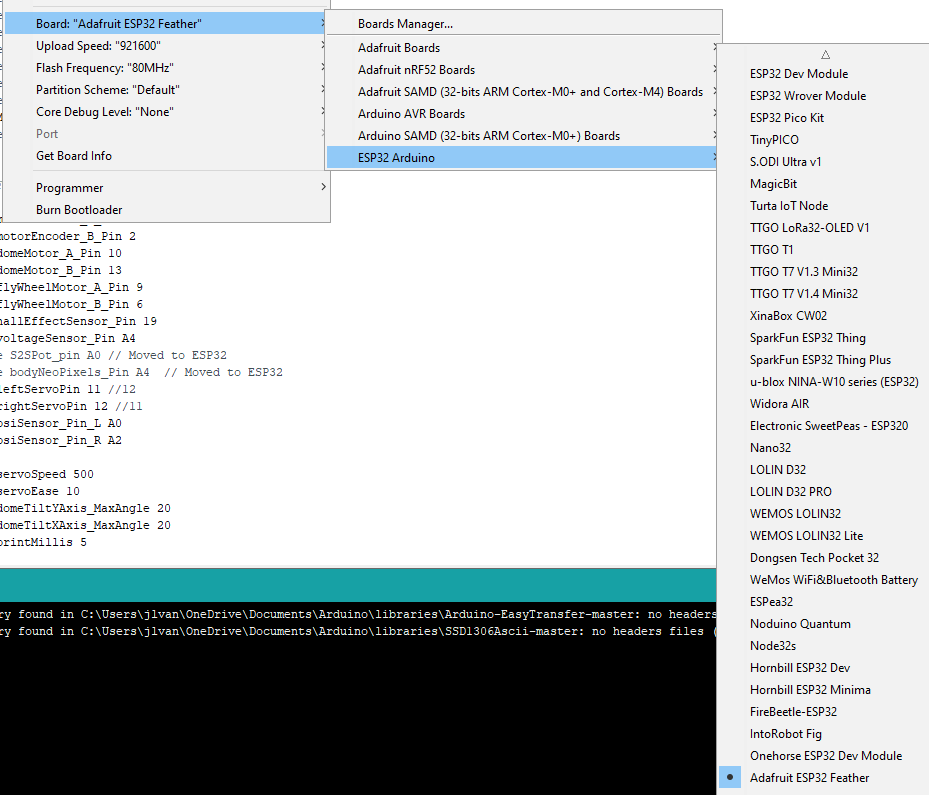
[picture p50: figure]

# Adding the ESP32 HUZZAH

Visit the repository and add to the IDE similar to how you added the Feather drivers

https://github.com/espressif/arduino-esp32#using-through-arduino-ide

The Additional Boards Manager URL: https://raw.githubusercontent.com/espressif/arduino-esp32/gh-pages/package_esp32_index.json

NOTE: if there are URLs you will need to add comma (, ) between each

Make sure you select versions and choose 1.06

NOTE: Anything newer than 1.06 is breaking on the Supporting PS3/4 controllers

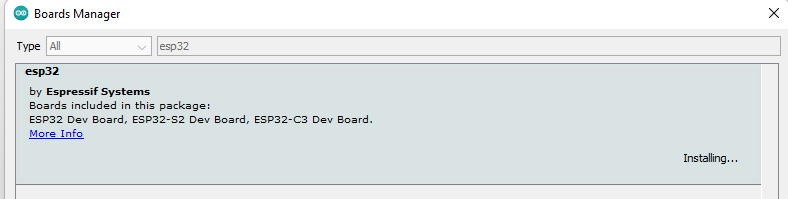
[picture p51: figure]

Will result in

Visit: https://www.silabs.com/developers/usb-to-uart-bridge-vcp-drivers

Download the Windows Driver and install

Debugging Stack traces

https://github.com/me-no-dev/EspExceptionDecoder

# Adafruit Trinket M0

Add the following IDE URI:

Choose Arduno SAMD and Adafruit SAMD boards and install latest

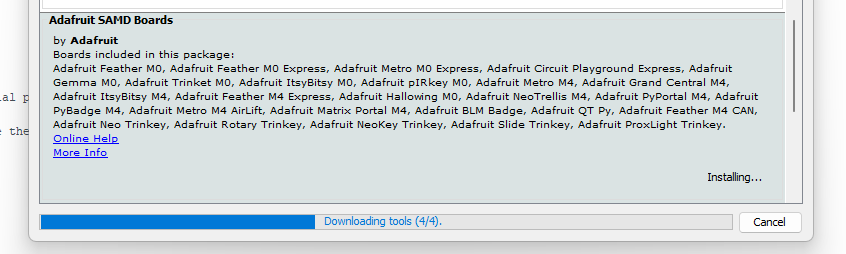
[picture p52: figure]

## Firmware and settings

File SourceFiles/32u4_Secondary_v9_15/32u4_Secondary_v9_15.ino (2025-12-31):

/*
 * Joe's Drive – V9.15
 * Secondary 32u4 feather – Dome Movement & PSI Lights
 * - Secondary Feather M0 Basic (SAMD21) Optional
 * - 32u4 Feather <--> ESP32 Huzzah on Serial1 (EasyTransfer)
 * - DFPlayer Mini via SoftwareSerial on A4(22)/D9 + BUSY on D10
 * - NeoPixel DIN on D13
 * - Dome Motor: PWM D3 (Timer3), DirA D5, DirB D6
 * - Servos: D11 (right), D12 (left)
 * - Hall: A2 (20)
 * - Encoder: choose INTERRUPT (D2/D4) or POLLING (A0/A1)
 *
 * Audio: Select one (#define AUDIO_SPARKFUN or #define AUDIO_DFPLAYER).
 * If neither is defined, AUDIO_NONE stubs compile & run silently.
 *
 * BOARDS: Install the Adafruit SAMD Library following this URL: 
 * https://learn.adafruit.com/adafruit-feather-m0-basic-proto/setup
 * Add the Adafruit SleepyDog Library for Watchdog replacement
 *
 */

 /*
  Feather 32u4 Pin Assignments
  Serial Communication
  Pin 0 (RX1) → ESP32 TX (EasyTransfer)
  Pin 1 (TX1) → ESP32 RX (EasyTransfer)

  DFPlayer Mini
  Pin D9 → DFPlayer TX (via voltage divider: 20 kΩ / 10 kΩ)
  Pin A4 → DFPlayer RX (via 1 kΩ series resistor)
  Pin D10 → DFPlayer BUSY (active LOW; INPUT_PULLUP or divider if BUSY = 5 V idle)

  NeoPixel
  Pin D13 → NeoPixel DIN (through SparkFun BOB‑12009 level shifter LV1 → HV1 → 330 Ω series resistor)
  BOB‑12009 LV → Feather 3.3 V
  BOB‑12009 HV → External 5 V rail
  GND → Common ground
  Power: External 5 V with 1000 µF capacitor across 5 V/GND near strip

  Encoder (NeveRest Classic 60)
  Phase A → D2 (interrupt source)
  Phase B → A0 (read inside ISR)
  Pull-ups: 4.7–10 kΩ to 3.3 V on A and B if encoder outputs are open-collector

  Hall Sensor
  Pin A2 → Hall sensor input (use INPUT_PULLUP)

  Dome Motor
  Pin D3 → PWM (Timer3)
  Pin D5 → Direction A
  Pin D6 → Direction B

  Servos
  Pin D11 → Right servo signal
  Pin D12 → Left servo signal

  Board Type Use
  You can comment out MODERNBOARD to utilize Legacy v8.2 board with i2c to SPARKFUN MP3 trigger
  Or v9.1b with major pin changes as mentioned above

  NOTE: Primary sketch can still run v9.1 always as it supports both boards 8.2 and 9.1

*/

// debugging the watch dog service...
// #define DEBUG_WATCHDOG
// #define DEBUG_32u4REC

// ------------------- FEATURE SWITCHES -------------------
#define MOVECONTROLLER
#define UseHallMonitor
#define MODERNBOARD // Comment this line for ALTERNATE compatibility - note must require Sparkfun MP3 trigger (i2c)

// Enable NeoPixel strip support:
#define USE_NEOPIXEL

// ---- AUDIO DEVICE SELECTION ----
// Uncomment ONE if you want sound:
// #define AUDIO_SPARKFUN        // SparkFun Qwiic MP3 Trigger (I2C) from 32u4
#define AUDIO_DFPLAYER          // DFPlayer Mini on SoftwareSerial pins 22 and 9 to be used with v8.9 Motherboard only



// Checks and balances for various definitions
#if defined(AUDIO_SPARKFUN) && defined(AUDIO_DFPLAYER)
  #error "Enable only one audio device: AUDIO_SPARKFUN or AUDIO_DFPLAYER"
#endif

// Require AUDIO_SPARKFUN
#if defined(AUDIO_DFPLAYER) && !defined(MODERNBOARD)
  #error "Enable only AUDIO_SPARKFUN AND do not use AUDIO_DFPLAYER"
#endif

// If neither device is selected, compile with no audio
#if !defined(AUDIO_SPARKFUN) && !defined(AUDIO_DFPLAYER)
  #define AUDIO_NONE
#endif

#if defined(MODERNBOARD) // Select one encoder method:
  #define ENCODER_METHOD_INTERRUPT // Use of pins D2 (INT1) + D4
#else
  #define ENCODER_METHOD_POLLING // use for v8.2 backwards compatibility on pins A0(18) + A1(19) for encoder
#endif



// ------------------- PIN DEFINITIONS (per your map) -------------------
/* DFPlayer Mini */
#if defined(AUDIO_DFPLAYER)  && defined(MODERNBOARD)
  #define DFPLAYER_TX_PIN   22    // Feather A4 (TX from Feather -> DFPlayer RX) through ~1kΩ
  #define DFPLAYER_RX_PIN   9     // Feather D9 (RX to Feather <- DFPlayer TX)
  #define DFPLAYER_BUSY_PIN 10    // Active LOW while playing (consider 10k pull-up to 5V)
  #define DFPLAYER_BAUD     9600
  #define AUDIO_DEFAULT_VOLUME 25
#endif

/* NeoPixel Strip */
#if defined(USE_NEOPIXEL)
  #define NEO_PIN           13    // DIN
  #define NEO_NUM_PIXELS    16    // <-- set to your actual count
#endif


/* Dome Motor (DFRobot Controller) */
#ifndef MODERNBOARD
#define domeMotor_pwm        10
#define domeMotor_pin_A      9
#define domeMotor_pin_B      6
#else
#define domeMotor_pwm        3    // PWM (Timer3)
#define domeMotor_pin_A      5    // Direction A
#define domeMotor_pin_B      6    // Direction B
#endif

/* Servos (HS-805BB x2) */
#define rightServo_pin       11   // Servo 1 signal
#define leftServo_pin        12   // Servo 2 signal

/* Hall Effect Sensor */
#define hallEffectSensor_Pin 20   // A2 (INPUT_PULLUP)

/* Encoder (NeveRest Classic 60) */
#if defined(ENCODER_METHOD_INTERRUPT)
  #define motorEncoder_pin_A 2    // Phase A -> D2 (INT1)
  #define motorEncoder_pin_B A0   // Phase B -> A0 (read inside ISR)
#elif defined(ENCODER_METHOD_POLLING)
  #define motorEncoder_pin_A 18   // A0 (PCINT7)
  #define motorEncoder_pin_B 19   // A1 (PCINT6)
#endif

// ------------------- CONSTANTS -------------------
#define servoSpeed                255
#define servoEase                 10
#define domeTiltYAxis_MaxAngle    12
#define domeTiltXAxis_MaxAngle    12
#define printMillis               100
#define leftServoOffset           -7
#define rightServoOffset           0
#define TICKS_PER_REV             1680
#define CENTER_TICK               878        // YOUR ACTUAL CENTER
#define MAX_ANGLE_TICKS           140
#define MP3_INIT_TIMEOUT          5000
#define SERVO_UPDATE_INTERVAL     5
#define DOME_CENTER_TIMEOUT       10000
#define HALL_DEBOUNCE             50
#define CENTER_TOLERANCE          15
#define MOTOR_SPEED               100
#define FIND_CENTER_SPEED         50
#define ENC_MIN_INTERVAL          500      // µs debounce
#define DRIFT_CHECK_INTERVAL      5000     // ms

// ---- AUDIO ABSTRACTION PROTOTYPES ----
bool audioInit(unsigned long timeoutMs = 5000);
void audioStop();
void audioPlay(uint16_t track);
bool audioIsPlaying();

// ------------------- LIBRARIES -------------------

#if defined(__AVR__)
  #include <VarSpeedServo.h>
  // VarSpeedServo myservo1, myservo2;
#elif defined(ARDUINO_ARCH_SAMD)
  #include <Servo.h>
  // Servo myservo1, myservo2;
#endif

#include <EasyTransfer.h>
#include <PID_v1.h>

#if defined(__AVR__)
// AVR-specific includes and code
#include <avr/wdt.h>
#define USE_AVR_WATCHDOG
#endif

#if defined(ARDUINO_ARCH_SAMD)
// SAMD-specific includes and code
#include <Adafruit_SleepyDog.h>
#define USE_SAMD_WATCHDOG
#endif


#if defined(AUDIO_SPARKFUN)
  #include <Wire.h>
  #include "SparkFun_Qwiic_MP3_Trigger_Arduino_Library.h"
  MP3TRIGGER mp3;                              // SparkFun object
  const uint8_t SPARKFUN_MP3_I2C_ADDR = MP3TRIGGER_ADDRESS; // default 0x37
#endif

#if defined(AUDIO_DFPLAYER)
  #include "DFRobotDFPlayerMini.h"
  #if defined(__AVR__)
  // AVR boards (32u4): Use SoftwareSerial on pins 9 (RX) and 22 (TX)
  #include <SoftwareSerial.h>
  SoftwareSerial mp3Serial(DFPLAYER_RX_PIN, DFPLAYER_TX_PIN); // RX, TX

  #elif defined(ARDUINO_ARCH_SAMD)
  // SAMD boards (Feather M0): Use hardware Serial1
  // Serial1 is mapped to pins 0 (RX) and 1 (TX) by default on Feather M0
  // But we need pins 9 and 22, so we use SERCOM remapping
  #include "wiring_private.h" // For pinPeripheral()

  #define DFPLAYER_RX_PIN 9   // RX from DFPlayer TX
  #define DFPLAYER_TX_PIN 22  // TX to DFPlayer RX

  Uart mp3Serial(&sercom3, DFPLAYER_RX_PIN, DFPLAYER_TX_PIN, SERCOM_RX_PAD_1, UART_TX_PAD_0);

  #endif

  DFRobotDFPlayerMini mp3;                   // DFPlayer object

#endif

#if defined(USE_NEOPIXEL)
  #include <Adafruit_NeoPixel.h>
#endif

// ------------------- GLOBALS -------------------
volatile long encPos = CENTER_TICK;
volatile unsigned long lastEncInterrupt = 0;

double Input_domeSpinServoPid, Output_domeSpinServoPid, Setpoint_domeSpinServoPid = 0;
int domeServoPWM;

#if defined(__AVR__)
  VarSpeedServo myservo1, myservo2;
#elif defined(ARDUINO_ARCH_SAMD)
  Servo myservo1, myservo2;
#endif

EasyTransfer recESP32, sendESP32;
PID myPID_domeSpinServoPid(&Input_domeSpinServoPid, &Output_domeSpinServoPid,
                           &Setpoint_domeSpinServoPid, 3.5, 0.8, 0.05, DIRECT);

int16_t leftServo_0_Position  = 70 + leftServoOffset;
int16_t rightServo_0_Position = 110 + rightServoOffset;
double leftServoPosition  = leftServo_0_Position;
double rightServoPosition = rightServo_0_Position;
double leftOldPosition    = leftServo_0_Position;
double rightOldPosition   = rightServo_0_Position;
double domeTiltAngle_X_Axis, domeTiltAngle_Y_Axis, leftStickY, leftStickX;

bool domeCenterSet = false, domeServoMode = false, enableDrive = false, reverseDrive = false;

// Shared audio state (visible to the whole sketch)
bool     sndplaying   = false;
int8_t   soundcmd     = 0;
uint16_t randomsound  = 0;  // will be set in audioInit()

unsigned long currentMillis, receiveMillis, lastPrintMillis, lastServoUpdateMillis;
unsigned long domeCenterStartMillis, lastHallLowMillis;
unsigned long lastDriftCheck = 0;
long lastStableEnc = CENTER_TICK;

#if defined(USE_NEOPIXEL)
  Adafruit_NeoPixel strip(NEO_NUM_PIXELS, NEO_PIN, NEO_GRB + NEO_KHZ800);
#endif

// ------------------- DATA STRUCTURES -------------------
struct RECEIVE_DATA_STRUCTURE {
  bool   driveEnabled;
  int8_t domeSpin;
  bool   moveL3;
  bool   moveR3;
  int8_t leftStickX;
  int8_t leftStickY;
  int8_t soundcmd;
  int8_t psiFlash;   // reuse for simple NeoPixel effect trigger
  float  pitch;
  float  roll;
} receiveFromESP32Data;


struct SEND_DATA_STRUCTURE {
  int16_t tiltAngle;       // Dome tilt angle (Y-axis or combined)
  bool    sndplaying;      // True if sound is playing
  int16_t lastSoundID;     // Last sound triggered
  int16_t domeDirection;   // Dome rotation direction (-1, 0, 1)
};
SEND_DATA_STRUCTURE sendToESP32Data;  // Global instance for sending status to ESP32
// struct SEND_DATA_STRUCTURE {
//   int16_t tiltAngle;
//   bool    sndplaying;
// } sendToESP32Data;

// ------------------- ENCODER ISR/Handlers -------------------
#if defined(ENCODER_METHOD_INTERRUPT)
// External interrupt on D2 (INT1), read Phase B on D4
void encoderISR() {
  unsigned long now = micros();
  if (now - lastEncInterrupt < ENC_MIN_INTERVAL) return;
  lastEncInterrupt = now;

  uint8_t a = digitalRead(motorEncoder_pin_A);
  uint8_t b = digitalRead(motorEncoder_pin_B);
  // Basic quadrature: if A changed, compare B for direction
  if (a == b) encPos++; else encPos--;
  encPos = (encPos % TICKS_PER_REV + TICKS_PER_REV) % TICKS_PER_REV;
}
#else
// Original PCINT on A0/A1 (polling inside ISR)
ISR(PCINT0_vect) {
  unsigned long now = micros();
  if (now - lastEncInterrupt < ENC_MIN_INTERVAL) return;
  lastEncInterrupt = now;

  static uint8_t lastState = 0;
  uint8_t a = digitalRead(motorEncoder_pin_A);
  uint8_t b = digitalRead(motorEncoder_pin_B);
  uint8_t state = (a << 1) | b;

  static const int8_t transitionTable[16] = {
    0, -1,  1,  0,
    1,  0,  0, -1,
   -1,  0,  0,  1,
    0,  1, -1,  0
  };

  int8_t delta = transitionTable[(lastState << 2) | state];
  if (delta != 0) {
    encPos += delta;
    encPos = (encPos % TICKS_PER_REV + TICKS_PER_REV) % TICKS_PER_REV;
  }
  lastState = state;
}
#endif

// ------------------- SETUP -------------------
void setup() {
 // Enable watchdog with ~4s timeout 
  #if defined(USE_AVR_WATCHDOG)
    wdt_enable(WDTO_4S);
  #elif defined(USE_SAMD_WATCHDOG)
    Watchdog.enable(4500);
  #endif

  pinMode(LED_BUILTIN, OUTPUT); // Optional heartbeat LED
  Serial.begin(115200);
  Serial1.begin(74880);           // ESP32 EasyTransfer

#if defined(USE_NEOPIXEL)
  strip.begin();
  strip.show(); // All off
#endif

  // Servos
  myservo2.attach(leftServo_pin);
  myservo1.attach(rightServo_pin);
  myservo2.write(leftServo_0_Position);
  myservo1.write(rightServo_0_Position);

  // EasyTransfer
  recESP32.begin(details(receiveFromESP32Data), &Serial1);
  sendESP32.begin(details(sendToESP32Data), &Serial1);

  pinMode(hallEffectSensor_Pin, INPUT_PULLUP);

  myPID_domeSpinServoPid.SetMode(AUTOMATIC);
  myPID_domeSpinServoPid.SetOutputLimits(-255, 255);

  pinMode(domeMotor_pwm,   OUTPUT);
  pinMode(domeMotor_pin_A, OUTPUT);
  pinMode(domeMotor_pin_B, OUTPUT);

#if defined(ENCODER_METHOD_INTERRUPT)
  pinMode(motorEncoder_pin_A, INPUT_PULLUP);
  pinMode(motorEncoder_pin_B, INPUT_PULLUP);
  attachInterrupt(digitalPinToInterrupt(motorEncoder_pin_A), encoderISR, CHANGE);
#else
  pinMode(motorEncoder_pin_A, INPUT_PULLUP);
  pinMode(motorEncoder_pin_B, INPUT_PULLUP);
  // Enable PCINT on A0 (PCINT7) and A1 (PCINT6)
  PCMSK0 |= (1 << PCINT7) | (1 << PCINT6);
  PCICR  |= (1 << PCIE0);
#endif

#ifdef UseHallMonitor
  domeCenterStartMillis = millis();
  // while (!domeCenterSet && millis() - domeCenterStartMillis < DOME_CENTER_TIMEOUT) {
  //   setDomeCenter();
  // }
  if (!domeCenterSet) Serial.println(F("Centering timeout"));
#else
  domeCenterSet = true;
  encPos = CENTER_TICK;
#endif

  Setpoint_domeSpinServoPid = 0;
  lastDriftCheck = millis();
  lastStableEnc = encPos;

  // ---- AUDIO INIT (unified) ----
  (void)audioInit(MP3_INIT_TIMEOUT);

  Serial.println(F("JOE'S DRIVE V9.15 — 32u4 SLAVE — SER — FULLY READY"));
}

// ------------------- MAIN LOOP -------------------
void loop() {
  // Reset watchdog every loop
  #if defined(USE_AVR_WATCHDOG)
    wdt_reset();
  #elif defined(USE_SAMD_WATCHDOG)
    Watchdog.reset();
  #endif

  Timechecks();
  SendRecieveData();
  DriftMonitor();  // Auto-snap to center

  if (enableDrive) {
    attemptDomeCentering();
    Servos();
    spinStuff();
    if (!domeCenterSet && domeServoMode && domeServoPWM == 0) setDomeCenter();
  }
  mp3play();

#if defined(USE_NEOPIXEL)
  neoUpdate();
#endif
}


void attemptDomeCentering() {
  if (!domeCenterSet && millis() - domeCenterStartMillis < DOME_CENTER_TIMEOUT) {
    setDomeCenter();
  } else if (!domeCenterSet) {
    Serial.println(F("Centering timeout"));
    domeCenterSet = true; // Fail-safe
  }
}

// ------------------- DRIFT MONITOR (AUTO-CORRECT) -------------------
void DriftMonitor() {
  if (millis() - lastDriftCheck >= DRIFT_CHECK_INTERVAL) {
    if (domeCenterSet && digitalRead(hallEffectSensor_Pin) == LOW && abs(encPos - lastStableEnc) < 3) {
      encPos = CENTER_TICK;  // Snap to center
      Serial.println(F("Drift corrected: snapped to 878"));
    }
    lastStableEnc = encPos;
    lastDriftCheck = millis();
  }
}

// ------------------- HALL CENTERING -------------------
void setDomeCenter() {
  if (digitalRead(hallEffectSensor_Pin) == LOW) {
    if (millis() - lastHallLowMillis >= HALL_DEBOUNCE) {
      domeCenterSet = true;
      encPos = CENTER_TICK;
      stopDome();
      Serial.println(F("Centered at 878"));
    }
    return;
  } else {
    lastHallLowMillis = millis();
  }

  double angleDiff = ((CENTER_TICK - encPos) % TICKS_PER_REV) * 360.0 / TICKS_PER_REV;
  if (angleDiff > 180) angleDiff -= 360;
  else if (angleDiff < -180) angleDiff += 360;

  if (abs(angleDiff) > (CENTER_TOLERANCE * 360.0 / TICKS_PER_REV)) {
    digitalWrite(domeMotor_pin_A, angleDiff > 0 ? HIGH : LOW);
    digitalWrite(domeMotor_pin_B, angleDiff > 0 ? LOW  : HIGH);
    analogWrite(domeMotor_pwm, FIND_CENTER_SPEED);
  } else {
    stopDome();
    if (abs(encPos - CENTER_TICK) <= CENTER_TOLERANCE) {
      domeCenterSet = true;
      encPos = CENTER_TICK;
    }
  }
}

// ------------------- DOME SPIN CONTROL -------------------
void spinStuff() {
  static bool lastMoveR3 = false;
  bool curR3 = receiveFromESP32Data.moveR3;
  if (curR3 != lastMoveR3) {
    domeServoMode = curR3;
    lastMoveR3 = curR3;
    if (domeServoMode) domeCenterSet = false;
  }

  if (domeServoMode) domeServoMovement();
  else               spinDome();
}

void spinDome() {
  int speed = abs(domeServoPWM) > 3 ? constrain(map(abs(domeServoPWM), 3, 127, 50, 255), 0, 255) : 0;
  if (domeServoPWM > 3 && enableDrive) {
    digitalWrite(domeMotor_pin_A, LOW);  digitalWrite(domeMotor_pin_B, HIGH);
    analogWrite(domeMotor_pwm, speed);
  } else if (domeServoPWM < -3 && enableDrive) {
    digitalWrite(domeMotor_pin_A, HIGH); digitalWrite(domeMotor_pin_B, LOW);
    analogWrite(domeMotor_pwm, speed);
  } else {
    stopDome();
  }
}

void domeServoMovement() {
  if (!domeCenterSet) { setDomeCenter(); return; }

  Setpoint_domeSpinServoPid = enableDrive
      ? constrain(map(domeServoPWM, -180, 180, -MAX_ANGLE_TICKS, MAX_ANGLE_TICKS),
                  -MAX_ANGLE_TICKS, MAX_ANGLE_TICKS)
      : 0;

  Input_domeSpinServoPid = ((encPos - CENTER_TICK) % TICKS_PER_REV);
  if (Input_domeSpinServoPid > TICKS_PER_REV/2) Input_domeSpinServoPid -= TICKS_PER_REV;
  else if (Input_domeSpinServoPid < -TICKS_PER_REV/2) Input_domeSpinServoPid += TICKS_PER_REV;

  myPID_domeSpinServoPid.Compute();

  int speed = abs(Output_domeSpinServoPid) > 0.5 ? constrain(abs(Output_domeSpinServoPid), 80, 255) : 0;
  if (Output_domeSpinServoPid > 0.5 && enableDrive) {
    digitalWrite(domeMotor_pin_A, LOW);  digitalWrite(domeMotor_pin_B, HIGH);
    analogWrite(domeMotor_pwm, speed);
  } else if (Output_domeSpinServoPid < -0.5 && enableDrive) {
    digitalWrite(domeMotor_pin_A, HIGH); digitalWrite(domeMotor_pin_B, LOW);
    analogWrite(domeMotor_pwm, speed);
  } else {
    stopDome();
  }
}

void stopDome() {
  digitalWrite(domeMotor_pin_A, LOW);
  digitalWrite(domeMotor_pin_B, LOW);
  analogWrite(domeMotor_pwm, 0);
}

// ------------------- TIME / COMMS -------------------
void Timechecks() {
  static unsigned long lastBlink = 0;
  if (millis() - lastBlink > 1000) {
    lastBlink = millis();
    digitalWrite(LED_BUILTIN, !digitalRead(LED_BUILTIN));
    #ifdef DEBUG_WATCHDOG
    Serial.println(F("[DEBUG] Loop alive")); // Heartbeat
    #endif
  }
  currentMillis = millis();
  receiveMillis = currentMillis;
  if (currentMillis - lastPrintMillis >= printMillis) {
    lastPrintMillis = currentMillis;
    debugRoutines();
  }
  // if (currentMillis - receiveMillis >= 1000 && enableDrive) enableDrive = false;
  
// Comm watchdog: disable drive if no data for >2s
  if (millis() - receiveMillis > 2000) {
    enableDrive = false;
    domeServoPWM = 0;
    soundcmd = 0;
  }

}


void SendRecieveData() {

  if (recESP32.receiveData()) {
    receiveMillis = currentMillis;
    enableDrive   = receiveFromESP32Data.driveEnabled;
    reverseDrive  = receiveFromESP32Data.moveL3;
    domeServoPWM  = map(receiveFromESP32Data.domeSpin, -127, 127, -180, 180);
    soundcmd      = receiveFromESP32Data.soundcmd;

    // Reset trigger
    if (soundcmd == -99) {
      Serial.println(F("[RESET] Command received from ESP32. Rebooting..."));
      wdt_enable(WDTO_15MS);
      while (1) {}
    }

    if (!enableDrive || !domeServoMode) {
      Setpoint_domeSpinServoPid = 0;
    }

    // Populate status for ESP32
    sendToESP32Data.tiltAngle     = (int16_t)domeTiltAngle_Y_Axis; // or combine X/Y if needed
    sendToESP32Data.sndplaying    = sndplaying;
    sendToESP32Data.lastSoundID   = soundcmd; // or track last played sound
    sendToESP32Data.domeDirection = (domeServoPWM > 3) ? 1 : (domeServoPWM < -3 ? -1 : 0);

    // Send status back
    sendESP32.sendData();
  }
}


// ------------------- AUDIO (unified) -------------------
void mp3play() {
  sndplaying = audioIsPlaying();

  // Only play if DFPlayer is idle
  if (soundcmd && !sndplaying) {
    if (soundcmd == 9) soundcmd = randomsound; // Random track
    audioPlay(soundcmd);
    soundcmd = 0;
  }
}
// void mp3play() {
//   sndplaying = audioIsPlaying();

//   if (soundcmd) {
//     if (soundcmd == 9) soundcmd = randomsound;  // keep your random behavior
//     if (sndplaying) audioStop();
//     audioPlay(soundcmd);
//     soundcmd = 0;
//   }
// }

// ------------------- NEOPIXEL (simple effect) -------------------
#if defined(USE_NEOPIXEL)
void neoUpdate() {
  // Basic activity: blink PSI based on enableDrive and domeServoPWM magnitude
  static uint32_t lastNeo = 0;
  if (millis() - lastNeo < 33) return;  // ~30 FPS max
  lastNeo = millis();

  uint8_t level = constrain(abs(domeServoPWM), 0, 127);
  uint32_t color = strip.Color(level, 0, 127 - level); // simple red/blue mix
  bool flash = (receiveFromESP32Data.psiFlash != 0);

  for (uint16_t i = 0; i < strip.numPixels(); i++) {
    if (flash && (i % 2 == ((millis()/200) % 2))) {
      strip.setPixelColor(i, strip.Color(255, 255, 255)); // flash white
    } else {
      strip.setPixelColor(i, color);
    }
  }
  strip.show();
}
#endif

// ------------------- SERVO TILT (SAFE SCALING) -------------------
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

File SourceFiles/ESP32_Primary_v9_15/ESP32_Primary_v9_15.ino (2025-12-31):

/*
 * JOE'S DRIVE - FINAL: S2S + PID BALANCE + 3-SEC CALIBRATION
 * ESP32 Primary v9.15 — enhanced ESPNOW mirroring with reliable send-queue
 * (Primary device)
 */

#include <Arduino.h>
#include <EasyTransfer.h>
#include <analogWrite.h>
#include <Preferences.h>
#include <PSController.h> // uses legacy 1.67 library of https://github.com/reeltwo/PSController
#include <Ticker.h>
#include <PID_v1.h>
#include <Wire.h>
#include <stdarg.h>   // va_list, va_start, va_end
#include <deque>      // ESPNOW send queue
#include "esp_task_wdt.h"  // enable watchdog service
#include "SoundMappings.h" // support sound mappings based on button presses etc
#include "ControllerDefs.h" // support for controllerdefs

/* --------------------ESPNOW Needed Libraries-----------*/
#include <WiFi.h>
#include <esp_now.h>
#include <esp_wifi.h>
#include <ArduinoOTA.h> // Add OTA updates for firmware

/* ------------------- CONFIG ------------------- */
const int  MAX_S2S_TILT       = 300;
const int  JOYSTICK_DEADZONE  = 25;
const int  S2S_POT_MIN        = 1300;
const int  S2S_POT_MAX        = 2150;
const int  POT_FILTER_SIZE    = 10;

bool REVERSE_S2S = false;    // Default
bool REVERSE_DRIVE = false;    // Default
bool USE_ESPNOW   = false;  // Default

bool DEBUG_CALIBRATION  = false;
bool DEBUG_JOYSTICK     = false;
bool DEBUG_S2S_MODE     = false;
bool DEBUG_MOTOR_OUTPUT = false;
bool DEBUG_IMU_RAW      = false;
bool DEBUG_ALL          = false;
bool DEBUG_COMPACT      = false;
bool debug32u4Status    = false; // Set to true to enable status debug

// ----- Feature toggles -----
bool ENABLE_DIAGNOSTIC_TELEMETRY = false;  // default OFF; toggle via "SET ENABLE_DIAGNOSTIC_TELEMETRY ON|OFF"
bool ENABLE_SMOOTH_BALANCE = false; // Default OFF

// ESPNOW remote MAC address
// Remote ESP32 MAC for ESPNOW (receiver): C4:5B:BE:90:6A:68
uint8_t remoteMAC[] = {0xC4, 0x5B, 0xBE, 0x90, 0x6A, 0x68};
const char* MASTER_NAV   = "7c:9e:bd:d7:63:c6";

/*------------------- OTA ESP32 Updates for firmware over Wifi--------------- */
String wifiSSID;
String wifiPassword;
bool OTA_ENABLED = false; // Dynamic OTA toggle

/* ------------------ RETURN-TO-CENTER TUNING --------------------------- */
const int  RETURN_DEADBAND   = 25;
const int  MIN_RETURN_PWM    = 30;
const int  MAX_RETURN_PWM    = 180;
bool ENABLE_ROLL_BIAS  = false;
const float ROLL_BIAS_GAIN   = 10.0;
const int defaultPOT         = 1708;


/* ----- PID GAINS (MUTABLE for tuning; persisted in Preferences) ----- */
float KP_PITCH = 45.0f;
float KI_PITCH = 0.8f;
float KD_PITCH = 12.0f;

/*
Pk2 = 45.0f;   // Lower P gain for gentle corrections
Dk2 = 1.0f;   // Moderate D gain for damping oscillations
Ik2 = 15.0f;    // Small I gain to avoid overshoot
PID2_S2S.SetTunings(Pk2, Ik2, Dk2);
*/

float Pk2 = 25.0f;
float Ik2 = 12.0f;
float Dk2 = 0.5f;

/* ----- IMU / Timing ----- */
const float IMU_DEADZONE   = 1.45;
const unsigned long IMU_TIMEOUT = 500;

/* ----- CALIBRATION HOLD ----- */
const unsigned long CALIB_HOLD_TIME = 3000;  // 3s
unsigned long calibHoldStart = 0;
bool calibSaveActive = false;
bool calibResetActive = false;

/* ------------------- PINS ------------------- */
const uint8_t S2S_PWM      = 33;
const uint8_t S2S_PIN_1    = 26;
const uint8_t S2S_PIN_2    = 25;
const uint8_t DRIVE_PWM    = 21;
const uint8_t DRIVE_PIN_1  = 4;
const uint8_t DRIVE_PIN_2  = 27;
const uint8_t S2S_POT_PIN  = 34;
const uint8_t FLYWHEEL_PWM = 15;
const uint8_t FLYWHEEL_PIN_A = 32;
const uint8_t FLYWHEEL_PIN_B = 14;

/* ------------------- STRUCTS ------------------- */
struct IMUData { float pitch, roll; };

struct Send32u4Data {
  bool   driveEnabled;
  int8_t domeSpin;
  bool   moveL3, moveR3;
  int8_t leftStickX, leftStickY;
  int8_t soundcmd, psiFlash;
  float  pitch, roll;
};

// ESPNOW struct for Dome communication
typedef struct struct_message {
  int psi;       // PSI trigger (0 or 1)
  byte btn;      // Optional button state
  float bat;     // Battery voltage from Dome
  int anim;      // Animation code (1–99)
} struct_message;

struct_message domeDataOut;  // Data we send to Dome
struct_message domeDataIn;   // Data we receive from Dome

struct Receive32u4Status {
  int domeTilt;        // Dome tilt angle or position
  bool soundPlaying;   // True if sound is currently playing
  int lastSoundID;     // Last sound triggered
  int domeDirection;   // Dome rotation direction (-1, 0, 1)
};

Receive32u4Status statusFrom32u4;
EasyTransfer recv32u4; // New EasyTransfer instance for receiving

/* ------------------- SOUND SYSTEM ------------------- */
// Moved to seperate support file SoundMappings.h

uint16_t pendingSound = SOUND_NONE;
static inline void emitSound(uint16_t track) { if (track != SOUND_NONE) pendingSound = track; }

#define EDGE_PRESSED(cur, prev) ((prev) == false && (cur) == true)

/* ------------------- LIVE TUNING MODE ------------------- */
enum class TuningSession { NONE, PITCH_KP, PITCH_KD, PITCH_KI, ROLL_PK, ROLL_DK, ROLL_IK };
TuningSession tuning = TuningSession::NONE;

unsigned long tuningHoldStart = 0;
bool tuningHoldActive = false;

float  kpPitchWork = 45.0f, kdPitchWork = 0.0f, kiPitchWork = 0.0f;
float  pk2Work     = 45.0f, dk2Work     = 0.0f, ik2Work     = 0.0f;

const float KP_STEP = 1.0f, KD_STEP = 1.0f, KI_STEP = 0.1f;
const float PK2_STEP = 1.0f, DK2_STEP = 1.0f, IK2_STEP = 0.1f;
const float REDUCE_FACTOR = 0.25f;

/* ------------------- GLOBALS ------------------- */
EasyTransfer recIMU, send32u4;
Preferences preferences;
PSController driveController(nullptr), domeController(nullptr);
Ticker mainLoopTicker;
Ticker telemetryTicker;


IMUData receiveIMUData;
Send32u4Data sendTo32u4Data;
ControllerButtons buttonsL, buttonsR;
bool IMUconnected = false, controllerConnected = false;
bool drivecontrollerConnected = false, domecontrollerConnected = false;
bool DomeServoMode = false, enableDrive = false, reverseDrive = false, EnableFlywheel = false;
bool autoBalance = false;
float flywheel = 0;
unsigned long lastIMUMillis = 0;
int potOffset = 1708;
float pitchOffset = 0.0, rollOffset = 0.0;
int potValues[POT_FILTER_SIZE];
int potValueIndex = 0;

unsigned long lastS2STime = 0;
unsigned long lastCompactDebug = 0;
const unsigned long COMPACT_DEBUG_INTERVAL = 100;

/* ------------------- AUTO-CENTER (BOOT) ------------------- */
bool autoCenterPending = true;
bool autoCenterDone     = false;
const float AUTO_CENTER_TOL_DEG      = 0.50f;
const unsigned long AUTO_CENTER_STABLE_MS = 1500;
unsigned long autoCenterStart = 0;

const int AUTO_POT_SAMPLES = 20;
int autoPotBuf[AUTO_POT_SAMPLES];
int autoPotIdx = 0;
bool autoPotFilled = false;
const float AUTO_POT_STD_MAX = 5.0f;

/* S2S Debug */
int lastPwmS2S = 0;
enum class S2SMode { JOY, RTN, STOP };
S2SMode s2sMode = S2SMode::STOP;

/* PID internals */
float pitchIntegral = 0.0;
float prevPitchError = 0.0;
unsigned long lastPIDTime = 0;
const float INTEGRAL_LIMIT = 100.0;

double Setpoint2 = 0.0;
double Input2 = 0.0;
double Output2 = 0.0;
double Output2_S2S_pwm = 0;
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

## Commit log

2021-05-13 Initial Changes focusing on the M0 board
    This is focusing on adding XBOX or MOVE awareness to the M0 code and debugging controller movements.
2021-05-21 Added support for replacing the M0 with ESP32
    This allows replacement of the M0 with a ESP32 HUZZAH32 Feather to support native wifi and BT for XBOX and PS3/4/5 controllers
    [ESP32_5.13_SimpleTransferUart_Move.ino]
2021-05-23 Adjusted the pins using GPIO eq for ESP32
    The ESP32 GPIO for the A0-A5 pins should work as long as I use the GPIO equivalents.
2021-05-23 Matching the ESP32 sends from MOVE controller
    Some slight tweaks to receive the move controller data from the ESP32 instead of the M0 and paired with Move Navigation Controllers.
2021-07-05 Consolidation of CPUs
    Validated ESP32 code for Trinket m0 and 32u4 connections
2021-07-05 Matched changes made to ESP32
    This matches required changes presented by the ESP32
2021-07-08 Update and rename ESP32_5.13_SimpleTransferUart_Move.ino to ESP32_7.7_SimpleTransferUart_Move.ino
    This now concludes the correct configuration of the pin usage to support the DFRobot Motor Driver, it requires 3 pins to work, PWM, and Logic1/2. Logic controls direction setting it to high or low, while PWM controls the speed applied to the direction. Setting both Logics to LOW stops.
2021-07-08 Update 32u4_7.21._SimpleTransferUart_Move.ino
    Completed support for PWM and Logic controls for the 32u4 working with the DFRobot Motor Driver
2021-07-08 Rename ESP32_7.7_SimpleTransferUart_Move.ino to ESP32_7.21_SimpleTransferUart_Move.ino
    Appended changes to branch
2021-07-08 Create ESP32_7.21_Wifi_Move.ino
    This adds the wifi access point to talk to the dome
2021-07-09 Create ESP32_7.21_dome.ino
    Completed the communications using ESPNOW between the 2 ESP32 between the BODY and the DOME simplified hardware requirements using 1 ESP32 HUZZAH, Battery, LEDs and a few Adafruit_NeoPixels.
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2021-07-09 Rename IMU_TrinketM0_Move.ino to TrinketM0_7.21_IMU.ino
    Renamed for proper formatting
2021-07-31 Update ESP32_7.21_Primary.ino
    Updated to work with v5.2 motherboard
2021-08-06 Update and rename TrinketM0_7.21_IMU.ino to TrinketM0_8.21_IMU.ino
    Working IMU/MPU Configuration along with 32u4 and Servo Control Validations
2021-08-06 Rename ESP32_7.21_Primary.ino to ESP32_8.21_Primary.ino
    Supports 32u4 and IMU Communications - validated
2021-08-06 Update TrinketM0_8.21_IMU.ino
    Completed Trinket board configuration - proper easytransfer of data
2021-12-28 Refreshed the code to support latest fixes
    This adds completed DFRobot Controls to the project
    Needs major overhaul for the ESP32 mapping to analogwrite calls
2021-12-28 Refreshed Code set for secondary feather
    This will need the following code completed:
    Head Spin and ENC/hall sensor checks for positioning
    Next: Lights and Sounds
2021-12-28 Refreshed to support latest board changes
    This now supports updated pins and configuration to support IMU via v6-v7 PCB board changes
2021-12-28 Update ESP32_1_22_Primary.ino
    Now have full drive controls for S2S, Drive, Gyro and Head Tilt
    Next: Dome Spin
2021-12-30 Updated Feather 32u4 Secondary code
    * Joe's Drive - V2 01/2022
    * Secondary 32u4 Dome Controls and PSI Body lights
    * Written by James VanDusen - https://www.facebook.com/groups/799682090827096
    * Utilizes Feather 32u4 Basic Proto From Adafruit: https://www.adafruit.com/product/2771
    *
    * Libraries Required
    * Feather 32u4 Board Libraries: https://learn.adafruit.com/adafruit-feather-32u4-basic-proto/using-with-arduino-ide
    * Encoder for the ENC on Dome Spin: https://github.com/PaulStoffregen/Encoder
    * Adafruit VS1053 Featherwing MusicPlayer: https://github.com/adafruit/Adafruit_VS1053_Library
    * Utilizes ESP32NOW technology over WiFi to talk between Dome and Body - need to captu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
2021-12-30 Refreshed Trinket (IMU)
    * Joe's Drive - V2 1/2022
    * Trinket IMU Dedicated board
    * You will need libraries:
    * EasyTransfer Library - https://github.com/madsci1016/Arduino-EasyTransfer
    * Adafruit MPU6050 - https://github.com/adafruit/Adafruit_MPU6050
    * Adafruit Common Sensor - https://github.com/adafruit/Adafruit_Sensor
    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
2021-12-30 Refreshed Dome ESP32 ESPNOW
    * Dome ESP32 HUZZAH32
    * AdafruitNeopixel: https://github.com/adafruit/Adafruit_NeoPixel
    * ESp32 Libraries: https://learn.adafruit.com/adafruit-huzzah32-esp32-feather/pinouts?view=all#using-with-arduino-ide
    * Utilizes ESP32NOW technology over WiFi to talk between Dome and Body - need to capture the Wifi MAC during bootup.
    * replace this with the mac of body uint8_t broadcastAddress[] = {0xFF, 0xFF, 0xFF, 0xFF, 0xFF, 0xFF};
    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
2022-01-05 Latest BOM to support all changes up to v7.1
    [JoesDrive_V2 BOM.xlsx]
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2022-01-21 Updated for Sound board support
    Provides necessary pin and diagrams to help builders understand changes between multiple options based on MP3 triggers being used.
2022-01-21 Completed Sparkfun MP3 trigger over i2c
    This code completes multiple combinations (left/right arrow key combos) with the Sparkfun MP3 trigger over i2c to the 32u4
2022-01-22 Performance Improvements
    Applied PINHD 2xpin rows to make it easier to solder
    Added GROVE connector for the 32u4 to support GROVE to JST or qwiic board adapters
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2022-02-01 Clarified CPU choices
    [JoesDrive_V2 BOM.xlsx]
2022-02-04 Standoffs for the buck converters
    [BUCKStandoffs v4.stl]
2022-02-09 This should allow for the JST XH
    connectors facing down
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2022-02-20 Updated to have correct Length M8 Bolts and Nuts
    Added Standard M8 nuts and 65mm Partially threaded Bolts
    [JoesDrive_V2 BOM.xlsx]
2022-02-20 Updated with Notes to Insert the M8 bolts
    Added important notes to add the M8s and added the start of the Center Piece connections to the swing arms
2022-02-23 Added optional power distribution fuse box
    [JoesDrive_V2 BOM.xlsx]
2024-01-14 Adjusted to support no MP3 player for testing
    This allowed commenting out NoMP3 to bypass checks on i2c addressing.
2024-01-19 Added DFPlayer Support
    Currently setup for v8 future board, will stage for use with secondary board to support v7.6
2024-01-19 Shadow Board v8.0 with support for DFPlayer
    *Changes
    Added DFPlayer mini onboard support as well as speaker outputs
    Removed 9v buck
    Added exposure to all pins on 32u4
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2024-03-21 Updated to correct James Orar issues
    This should correct the issues seen where there is no Dome arm movements or GYRO
2024-04-06 Updated Primary ESP32 Drive controls
    This now supports ramping and S2S deadzone controls
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2024-04-14 Corrected filtering and dome spin
2024-04-18 Stability improvements
    Added smoother servo controls and proper mapping to MOVE controller
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2024-05-27 added error corrections
    For flywheel and domespin controls using L1 and R1 buttons
2025-12-01 Supports V3 Design with backwards support
    This is new revamped drive system with either chain or gear based drive train(s)
    [BatteryHarness Cover.stl, BatteryHarness.stl, Coupler.stl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]
2025-12-05 i2C code to support PCB 8.9b or c
    This is inter board communications to support adapting the DFplayer mini to the 32u4 board to allow MP4 playing as well as offer configuration, tuning and changes to be applied off first boot state o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
    ESP32_Primary_v8_9b_i2c_RC
    32u4_Secondary_v8_9b_i2c_RC
2025-12-07 Corrected STL files from drawing
    [HeadTiltCoupler.stl, HeadTiltCouplerPin_x2.stl, HeadTiltMotorCoupler.stl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]
2025-12-31 Final PCB for Joes Drive V2 Complete
    Allows for multiple choices for MP3, 32u4 or M0 basic feathers and proper DFplayer mini support. Also provides much needed voltage support for signals to encoder, DFPlayer and other peripherals.
2025-12-31 Version 9.15 bumped
    This has major updates including live PID tuning, ability to restore and save states, bootup sequences, stability enhancements and DFplayer support for PCB 9.15
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2025-12-31 Updated supporting many changes
    Allows for gear versus chain drives, allows for replacement parts from discontinued parts.
    [JoesDrive_V2 BOM.xlsx]
2025-12-31 Supported discontinued parts
    And enhanced replacement parts
    [BatteryHarness Cover.stl, CouplerPin_v2.stl, CouplerScrew_v2.stl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]
2025-12-31 Supports latest PCBs
    Updated code to support boards
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2026-01-14 Adjusted and enhancements for coupler and tilt
    This helps/aids with better assembly and securing the parts together
